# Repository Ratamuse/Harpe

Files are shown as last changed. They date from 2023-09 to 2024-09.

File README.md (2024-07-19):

# Harpe anti frelons à pattes jaunes

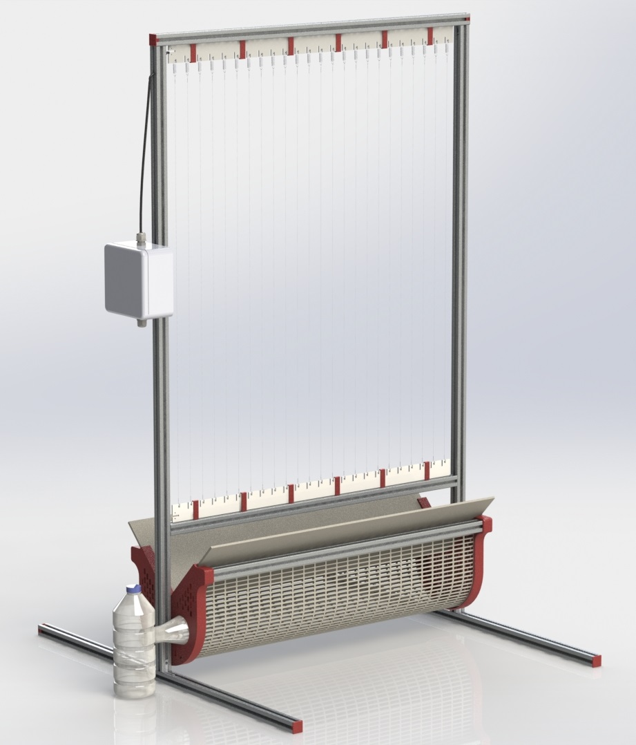
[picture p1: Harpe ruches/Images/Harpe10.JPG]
This is an image


La construction de cette harpe fait suite à différents essais effectués les années passées. Montage en tubes PVC, armature en bois, bac de noyade. Ces solutions, certes peu chères, ne me satisfaisaient pas. Manque de rigidité, vieillessement prématuré, problème de cours circuits, noyades d'insectes et d'abeilles en pagaille etc etc. 
Ce montage n'est pas "LOW COST" et ne peux rivaliser avec les montages fait à partir de tréteaux, tuyaux de récupération ou autre. C'est une compilation de ce qui existe déjà, avec des améliorations et les plans sont disponibles si vous voulez en construire une.  
Ayant eu des soucis de cours circuits par le passé, j'ai ajouté un microntroleur avec capteur de luminosité et d'humidité afin de couper le montage la nuit et lorsque l'humidité est trop forte. 

Vous trouverez ci dessous les liens pour:

- [Liste du materiel](https://github.com/Ratamuse/Harpe/blob/main/Harpe%20ruches/Materiel/Materiel.md)
- [Fichier .STL pour impression 3D](https://github.com/Ratamuse/Harpe/tree/main/Harpe%20ruches%2FFichiers%203d%20%C3%A0%20imprimer)
- [Aide au montage](https://github.com/Ratamuse/Harpe/blob/main/Harpe%20ruches/Montage/Construction.md)
- [Fichiers nécessaires pour fabriquer le circuit imprimé de la harpe](https://github.com/Ratamuse/Harpe/tree/main/Harpe%20ruches/Fichier%20Kicad)
- [Exemple de montage électrique](https://github.com/Ratamuse/Harpe/blob/main/Harpe%20ruches/Fichier%20Kicad/Harpe_ESP32/PCB.md)
- [Programme pour microcontroleur ESP32](https://github.com/Ratamuse/Harpe/tree/main/Harpe%20ruches/Code%20Arduino)

**Support via PayPal (https://paypal.me/GNUVarioE?country.x=FR&locale.x=fr_FR) Cette harpe vous plait et est efficace. Payez moi un café! ;-) Support via PayPal (https://paypal.me/GNUVarioE?country.x=FR&locale.x=fr_FR)**

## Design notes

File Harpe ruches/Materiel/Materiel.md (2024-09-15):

## Harpe

Dimensions

**Profilés aluminium extrudé 2020 B-Type rainure 6**
- 2x 1050mm
- 2x 500mm
- 1x 660mm
- 1x 620mm

**Fixation:**
- 8x Équerres interne 20 B-Type rainure 6, M5
- 2x tasseaux lourds, B-Type rainure 6, M5
- 2x Vis DIN 912 M5x12

**Impression 3D:**
- 2x capuchons haut
- 4x capuchons bas
- 6x coulisseaux circuit imprimé haut
- 6x coulisseaux longs circuit imprimé bas
- 1x boîte de jonction (si pas boîte du commerce)

**Partie fils**
- 1x circuits imprimés 600mm 24 trous 4 couches
- 1x circuits imprimés 600mm 24 trous crochets
- 24x ressorts d'extension 5x10x0.5mm
- 1x Bobine de fil inox 0.3mm (fil à filer les cadres)

**Partie électrique**
- 1x Boîte de jonction IP55 minimum 115x115x60mm
- 1x Module haute tension 4.2v --> 1800v
- 1x Convertisseur de tension 12V --> 4.2V
- 2x connecteurs WAGO 2 fils
- Câble électrique 2x1.5mm2
- Fer à braser et fil de soudure
- Scotch isolant
- Batterie 12 volts

## Bac de récupération

**Profilés aluminium extrudé 2020 B-Type rainure 6**
- 2x 610mm

**Impression 3D**
- 1x flasque
- 1x flasque "bouteille"

**Fixation:**
- 4x tasseaux lourds, B-Type rainure 6, M5
- 4x Vis DIN 912 M5x12

**Divers**
- 2x grilles à reine Nicot Dadant 10C
- 10x colliers de serrage
- 2x planches 610x200x3mm (bois, PVC, bakélite....)
- 1x bouteille vide style "Badois" ou "San Pelegrino"
- 1x bouteille vide style "Volvic" ou "Cristaline"

## Option panneau solaire
- 1x panneau solaire 10W
- 1x chargeur solaire PWM ou mieux MPPT
- 1x batterie 12V 7AH

## Kit (seulement profilés aluminium et visserie) disponible en achat sur le site Motedis.fr en cliquant sur le lien suivant:

**[Kit permettant de construire une harpe](https://www.motedis.fr/shop/create_offers_kit.php?oID=809841)**

Cliquez sur "ok" fenêtre "Langue/Paramètres régionaux" puis allez sur panier. Vous pouvez choisir le nombre de kits à commander en haut de la liste. 
Vous restez libre d'enlever du panier l'item "Idea fee". Cela est proposé par le site pour rénumérer la personne qui à préparé le kit. Il existe d'autres sites pour commander des profilés, je ne suis pas affilié et n'ai aucun intéret avec cette société.

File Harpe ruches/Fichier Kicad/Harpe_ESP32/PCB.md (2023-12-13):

# Carte d'alimentation jusqu'à six harpes:

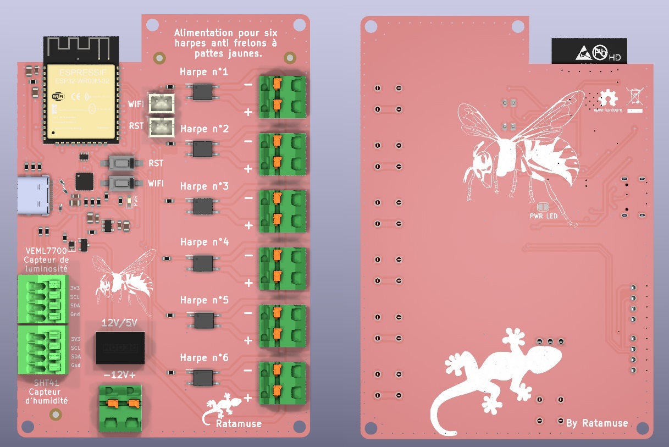
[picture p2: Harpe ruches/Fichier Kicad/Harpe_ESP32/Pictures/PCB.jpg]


La carte doit être alimentée par une batterie 12V. Elle permet d'alimenter de manière cyclique jusqu'à six harpes afin d'économiser de l'énergie et moins soliciter les modules haute tension. 
La carte est équipée de deux connecteurs permettant de brancher:
* un capteur d'humidité SHT41 permettant de couper l'alimentation des harpes en cas de forte humidité.
* un capteur de luminosité permettant de couper les harpes la nuit. 

Les valeurs limites de luminosité, humidité, le nombre de harpes et le rapport cyclique d'alimentation sont modifiables via un serveur web embarqué. 
Pour y accéder il suffit d'appuyer deux secondes sur le bouton "WIFI" (sur la carte ou déporté). Le réseau "harpes" apparaitra comme point d'accès wifi. Le mot de passe pour s'y connecter est 123456789 
Une fois les valeurs modifiées, la carte redemarrera avec les nouveaux paramètres en appuyant sur le bouton "Enregistrer".

Les modules haute tension des harpes consommant en permanence 0.1A, cette manière de les alimenter permet de n'utiliser qu'une petite batterie de 12V 7AH et un panneau solaire de 10W. Un régulateur de charge solaire PWM de 12V, 5 ou 10A sera nécessaire pour recharger la batterie.  

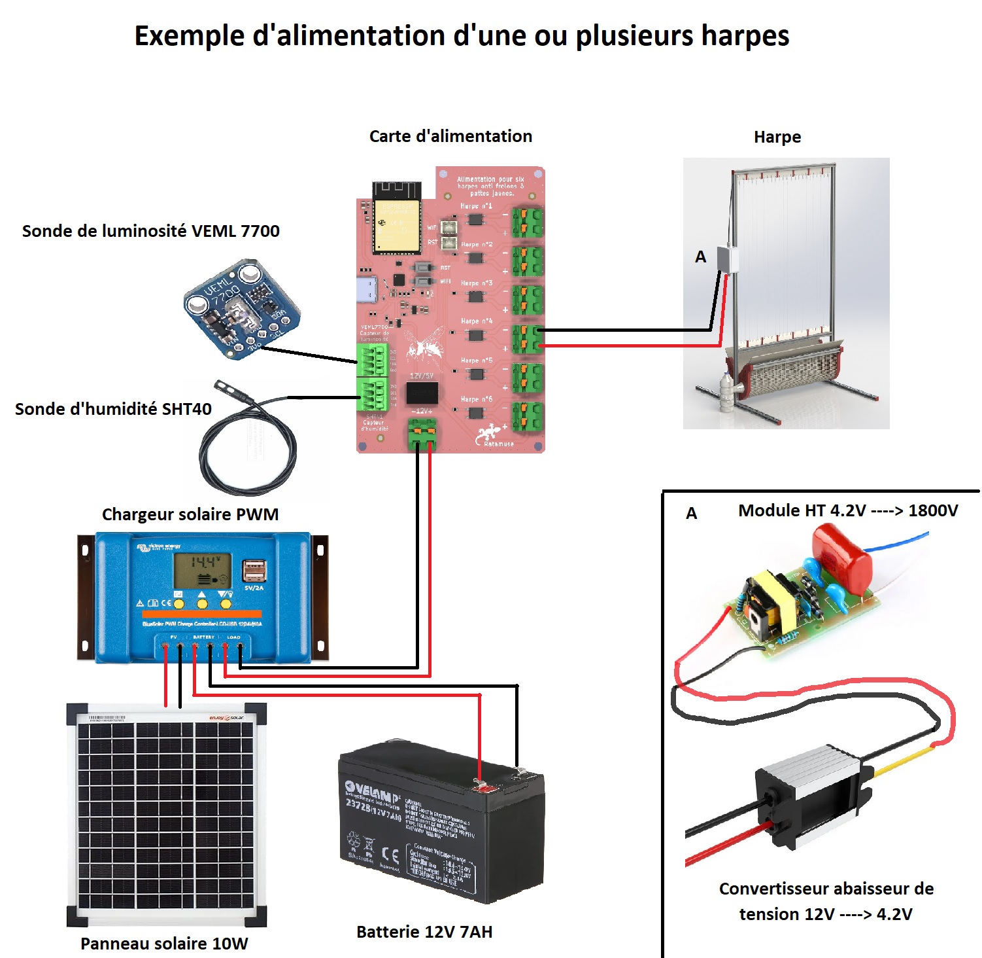
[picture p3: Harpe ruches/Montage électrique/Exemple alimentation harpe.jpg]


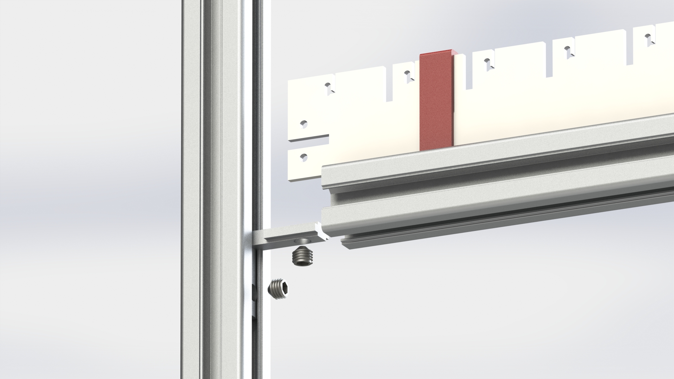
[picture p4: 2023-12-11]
Harpe ruches/Images/Harpe5bis.JPG

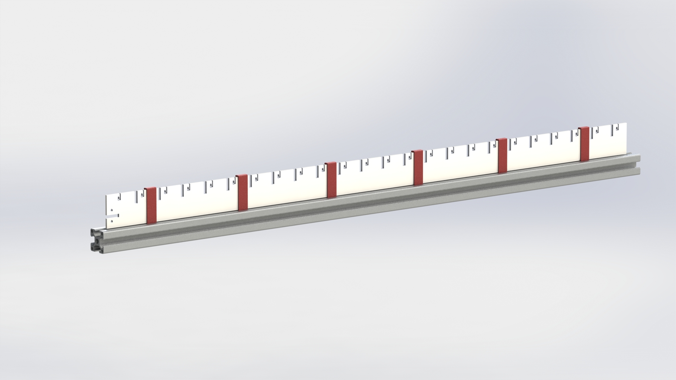
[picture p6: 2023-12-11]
Harpe ruches/Images/Harpe2bis.JPG

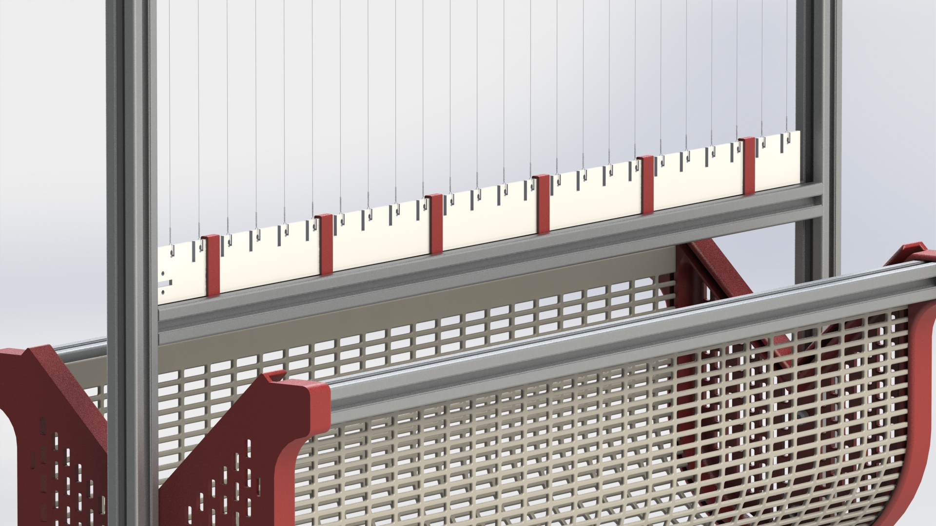
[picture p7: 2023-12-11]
Harpe ruches/Images/Harpe6bis.JPG

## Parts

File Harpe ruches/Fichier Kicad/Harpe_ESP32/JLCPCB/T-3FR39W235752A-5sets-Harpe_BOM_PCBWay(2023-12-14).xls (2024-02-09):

PCBWay Bom Quotation, Product No.:T-3FR39W235752A
Item # | *Designator | *Qty | Manufacturer | *Mfg Part # | Description / Value | *Package/Footprint | *Unit Price(5 sets) | *Total | *Delivery Time | Customer Reply | PCBWay Update
1 | C1,C3 | 2 | Murata | GRM219R61C226ME15L | 16V 22uF X5R ±20% 0805 Multilayer Ceramic Capacitors MLCC | C_0805_2012Metric | $0.291 | $2.910
2 | C2,C7,C9,C11 | 4 | Murata | GCJ188R71C104KA01D | MLCC - CMS 0.1 uF 16 VDC 10% 0603 X7R | C_0603_1608Metric | $0.054 | $1.080
3 | C6 | 1 | Murata | GCM21BR71C475KA73L | MLCC - CMS 4.7 uF 16 VDC 10% 0805 X7R | C_0805_2012Metric | $0.155 | $0.775
4 | R1,R19,R29,R8,R37 | 5 | YAGEO | RT0603BRD0710KL | 100mW Thin Film Resistor ±25ppm/℃ ±0.1% 10kΩ 0603 Chip Resistor - Surface Mount ROHS | R_0603_1608Metric | $0.118 | $2.950
5 | R2,R3,R4,R5,R6,R7,R14 | 7 | YAGEO | RT0603BRD071KL | 100mW Thin Film Resistor ±25ppm/℃ ±0.1% 1kΩ 0603 Chip Resistor - Surface Mount ROHS | R_0603_1608Metric | $0.095 | $3.325
6 | R12 | 1 | YAGEO | RT0603BRD0722K1L | 100mW Thin Film Resistor ±25ppm/℃ ±0.1% 22.1kΩ 0603 Chip Resistor - Surface Mount ROHS | R_0603_1608Metric | $0.147 | $0.735
7 | R13 | 1 | YAGEO | RT0603BRD0747K5L | 100mW Thin Film Resistor ±25ppm/℃ ±0.1% 47.5kΩ 0603 Chip Resistor - Surface Mount ROHS | R_0603_1608Metric | $0.147 | $0.735
8 | U1 | 1 | Espressif | ESP32-WROOM-32E-N4 | ESP32-WROOM-32E-N4 | SMD,18x25.5mm | $4.543 | $22.715
9 | U2,U3,U4,U5,U6,U7 | 6 | Omron Electronics | G3VM-61VY2 |  | SOP254P960X420-4N | $1.030 | $30.900
10 | U12 | 1 | SILICON LABS | CP2102N-A02-GQFN24R | USB转UART UART QFN-24-EP(4x4) USB ICs ROHS | QFN-24-1EP_4x4mm_P0.5mm_EP2.6x2.6mm | $3.140 | $15.700
11 | U13 | 1 | Torex Semicon | XC6220B331MR-G |  | SOT-23-5 | $0.645 | $3.225
12 | R16,R17 | 2 | YAGEO | AT0603BRD072K2L | 100mW Thin Film Resistor ±25ppm/℃ ±0.1% 2.2kΩ 0603 Chip Resistor - Surface Mount ROHS | R_0603_1608Metric | $0.103 | $1.030
13 | D4 | 1 | STMicroelectronics | BAT20JFILM |  | D_SOD-323 | $0.163 | $0.815
14 | Q1 | 1 | ROHM Semicon | UMH3NTN | 100@1mA,5V 2 NPN - Pre-Biased 150mW 100mA 50V SOT-363 | SOT-363_SC-70-6 | $0.114 | $0.570
15 | Q2 | 1 | Diodes Incorporated | DMG2301L-7 | 20V 3A 1.5W 120mΩ@4.5V,2.8A 1.2V@250uA P Channel SOT-23 MOSFETs ROHS | SOT-23 | $0.151 | $0.755
16 | D1,D2,D3 | 3 | Littelfuse | SP1003-01DTG | 7A@8/20us 12V@(Typ) 6V Unidirectional 5V@Max SOD-723 TVS ROHS | SODFL1406X65N | $0.099 | $1.485
17 | J13 | 1 | GCT | USB4105-GF-A | Connectors USB USB Type C,2.0, Rec,SMT, 0.95mmTH Shell Stakes,G/F,RA,Top Mnt,T&R | USB_C_Receptacle_USB2.0 USB4105-GF-A | $1.497 | $7.485
18 | R26 | 1 | YAGEO | RT0603FRE071ML | 100mW Thin Film Resistor ±50ppm/℃ ±1% 1MΩ 0603 Chip Resistor - Surface Mount ROHS | R_0603_1608Metric | $0.084 | $0.420
19 | R33,R34 | 2 | YAGEO | RT0603BRD075K1L | 100mW Thin Film Resistor ±25ppm/℃ ±0.1% 5.1kΩ 0603 | R_0603_1608Metric | $0.094 | $0.940
20 | D15 | 1 | XINGLIGHT | XL-1608VRC-06 | 90mcd 红色透镜 615nm~630nm 正贴 Red 120° 75mW 0603 Light Emitting Diodes (LED) ROHS | LED_0603_1608Metric_Castellated | $0.103 | $0.515
21 | C24,C25 | 2 | Murata | GRM21BR61C106KE15K | 16V 10uF X5R ±10% 0805 Multilayer Ceramic Capacitors MLCC - SMD/SMT ROHS | C_0805_2012Metric | $0.054 | $0.540
 |  |  |  |  |  |  | Component Cost | $99.60
 |  |  |  |  |  |  | Assembly Cost | $30.00
 |  |  |  |  |  |  | PCB Cost | $5.00
 |  |  |  |  |  |  | V1 Member 1% off | -$0.35
 |  |  |  |  |  |  | All Total 5 Sets | $134.25

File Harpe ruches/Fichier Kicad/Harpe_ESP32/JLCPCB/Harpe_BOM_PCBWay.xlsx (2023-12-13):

 |  |  | xxxx xxxx xxxxx xxPCS BOM (Sample Bill of Materials)
Item # | *Designator | *Qty | Manufacturer | *Mfg Part # | Description / Value | *Package/Footprint | Type | Your Instructions / Notes
1 | C1,C3 | 2 | Murata | GRM219R61C226ME15L | 16V 22uF X5R ±20% 0805 Multilayer Ceramic Capacitors MLCC | C_0805_2012Metric
2 | C2,C7,C9,C11 | 4 | Murata | GCJ188R71C104KA01D | MLCC - CMS 0.1 uF 16 VDC 10% 0603 X7R | C_0603_1608Metric
3 | C6 | 1 | Murata | GCM21BR71C475KA73L | MLCC - CMS 4.7 uF 16 VDC 10% 0805 X7R | C_0805_2012Metric
4 | R1,R19,R29,R8,R37 | 5 | YAGEO | RT0603BRD0710KL | 100mW Thin Film Resistor ±25ppm/℃ ±0.1% 10kΩ 0603 Chip Resistor - Surface Mount ROHS | R_0603_1608Metric
5 | R2,R3,R4,R5,R6,R7,R14 | 7 | YAGEO | RT0603BRD071KL | 100mW Thin Film Resistor ±25ppm/℃ ±0.1% 1kΩ 0603 Chip Resistor - Surface Mount ROHS | R_0603_1608Metric
6 | R12 | 1 | YAGEO | RT0603BRD0722K1L | 100mW Thin Film Resistor ±25ppm/℃ ±0.1% 22.1kΩ 0603 Chip Resistor - Surface Mount ROHS | R_0603_1608Metric
7 | R13 | 1 | YAGEO | RT0603BRD0747K5L | 100mW Thin Film Resistor ±25ppm/℃ ±0.1% 47.5kΩ 0603 Chip Resistor - Surface Mount ROHS | R_0603_1608Metric
8 | U1 | 1 | Espressif | ESP32-WROOM-32E-N4 | ESP32-WROOM-32E-N4 | SMD,18x25.5mm
9 | U2,U3,U4,U5,U6,U7 | 6 | Omron Electronics | G3VM-61VY2 |  | SOP254P960X420-4N
10 | U12 | 1 | SILICON LABS | CP2102N-A02-GQFN24R | USB转UART UART QFN-24-EP(4x4) USB ICs ROHS | QFN-24-1EP_4x4mm_P0.5mm_EP2.6x2.6mm
11 | U13 | 1 | Torex Semicon | XC6220B331MR-G |  | SOT-23-5
14 | R16,R17 | 2 | YAGEO | AT0603BRD072K2L | 100mW Thin Film Resistor ±25ppm/℃ ±0.1% 2.2kΩ 0603 Chip Resistor - Surface Mount ROHS | R_0603_1608Metric
15 | D4 | 1 | STMicroelectronics | BAT20JFILM |  | D_SOD-323
16 | Q1 | 1 | ROHM Semicon | UMH3NTN | 100@1mA,5V 2 NPN - Pre-Biased 150mW 100mA 50V SOT-363 | SOT-363_SC-70-6
17 | Q2 | 1 | Diodes Incorporated | DMG2301L-7 | 20V 3A 1.5W 120mΩ@4.5V,2.8A 1.2V@250uA P Channel SOT-23 MOSFETs ROHS | SOT-23
18 | D1,D2,D3 | 3 | Littelfuse | SP1003-01DTG | 7A@8/20us 12V@(Typ) 6V Unidirectional 5V@Max SOD-723 TVS ROHS | SODFL1406X65N
19 | J13 | 1 | GCT (https://www.mouser.fr/manufacturer/gct/) | USB4105-GF-A | Connectors USB USB Type C,2.0, Rec,SMT, 0.95mmTH Shell Stakes,G/F,RA,Top Mnt,T&R | USB_C_Receptacle_USB2.0 USB4105-GF-A
20 | R26 | 1 | YAGEO | RT0603FRE071ML | 100mW Thin Film Resistor ±50ppm/℃ ±1% 1MΩ 0603 Chip Resistor - Surface Mount ROHS | R_0603_1608Metric
21 | R33,R34 | 2 | YAGEO | RT0603BRD075K1L | 100mW Thin Film Resistor ±25ppm/℃ ±0.1% 5.1kΩ 0603 | R_0603_1608Metric
22 | D15 | 1 | XINGLIGHT | XL-1608VRC-06 | 90mcd 红色透镜 615nm~630nm 正贴 Red 120° 75mW 0603 Light Emitting Diodes (LED) ROHS | LED_0603_1608Metric_Castellated
23 | C24,C25 | 2 | Murata | GRM21BR61C106KE15K | 16V 10uF X5R ±10% 0805 Multilayer Ceramic Capacitors MLCC - SMD/SMT ROHS | C_0805_2012Metric
Need a quick and accurante quote? Need an efficient production? Please read SMT Ordering Necessary Files & Info in 1 minute. Thank you very much! (https://www.pcbway.com/smt_ordering_guide.html)
Click for Instructions on How to Create a BOM (https://www.pcbway.com/blog/PCB_Assembly/How_to_Build_a_BOM__Bill_Of_Materials_.html)

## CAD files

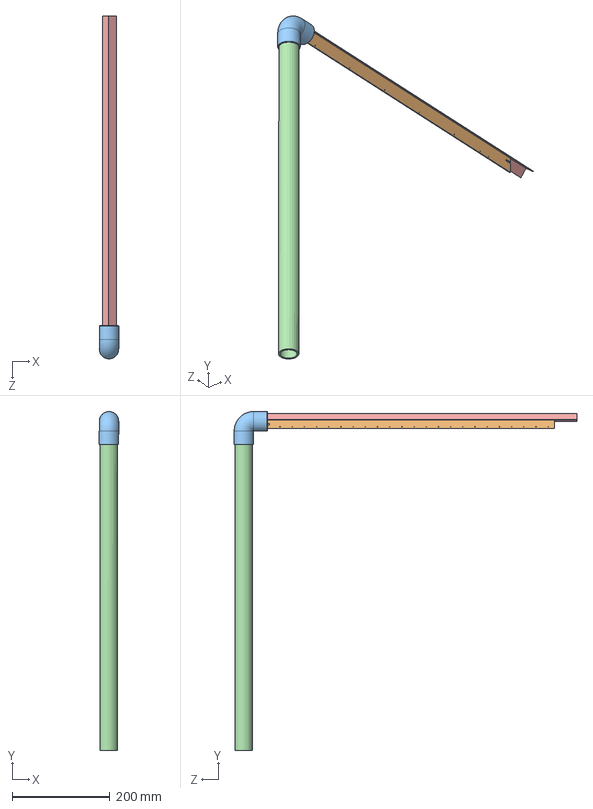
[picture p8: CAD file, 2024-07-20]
Harpe ruches/Fichier Kicad/Harpe ruches bas sans cuivre/Harpe.SLDASM
40.1 x 695.2 x 702.9 mm
fixation pcb ruche
Harpe ruches
tube 32 x600
equerre_egale_635

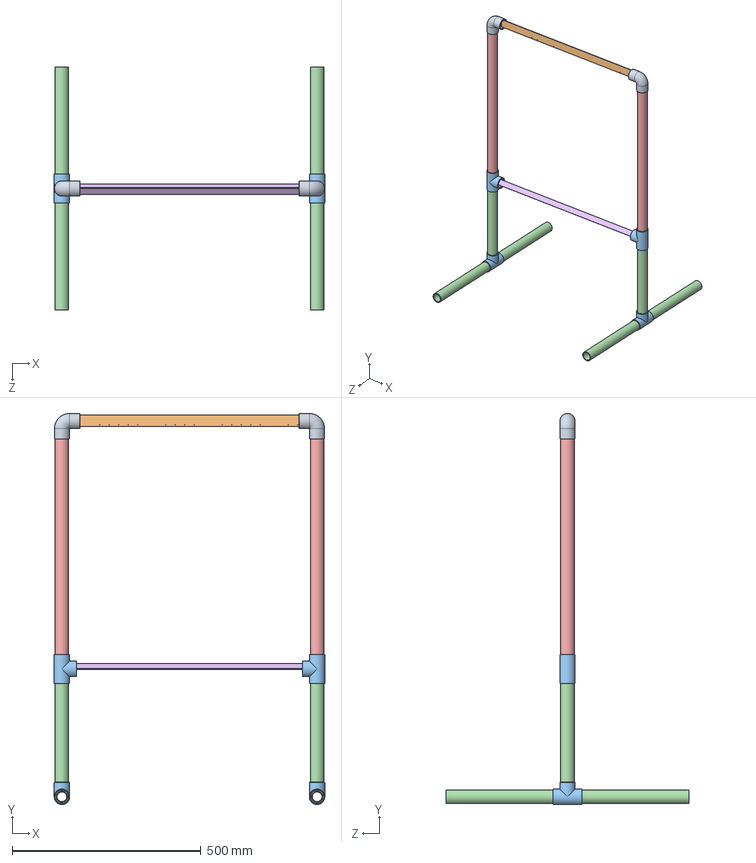
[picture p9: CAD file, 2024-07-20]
Harpe ruches/Fichier Kicad/Harpe ruches bas sans cuivre/harpe frelon/Harpe 2.0.SLDASM
717.7 x 1037.2 x 644.0 mm
PCB harpe
tube 32 x250 x 6
tube 32 x600 x 2
equerre_egale_635

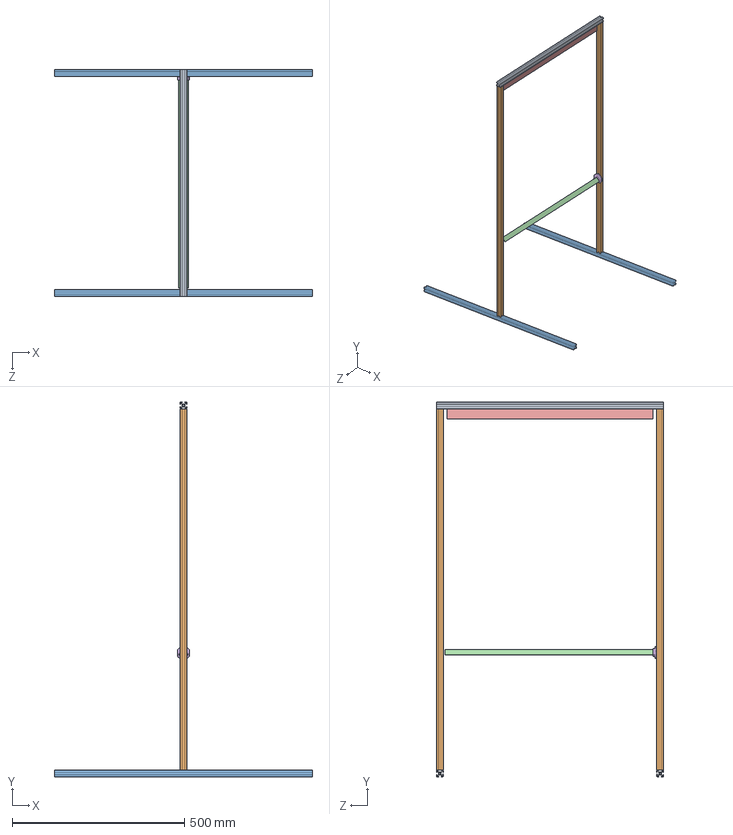
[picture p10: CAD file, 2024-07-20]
Harpe ruches/Fichier Kicad/Harpe ruches bas sans cuivre/harpe frelon/harpe alu/Harpe_V3.SLDASM
750.0 x 1090.0 x 660.0 mm
profilé 660x20
profilé 1050x20 x 2
profilé 750x20 x 2
equerre_egale_620x2
pcb 600x30x2
accroche equerre

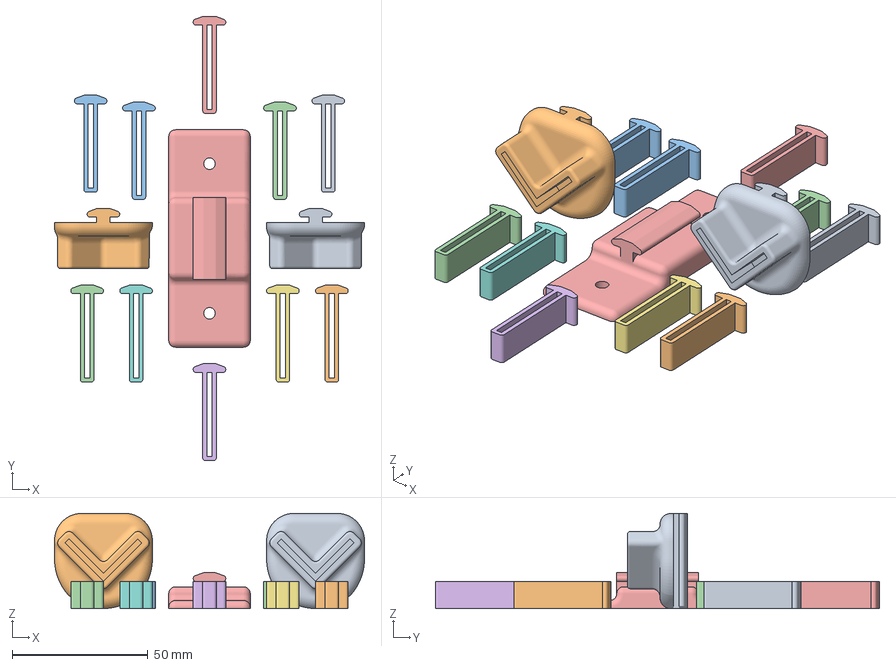
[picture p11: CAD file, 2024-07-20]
Harpe ruches/Fichier Kicad/Harpe ruches bas sans cuivre/harpe frelon/harpe alu/Kit ruche blanc_equerre & PCB.3mf
114.0 x 163.4 x 35.0 mm
accroche equerre.STL
accroche pcb.STL
support boite harpe.STL

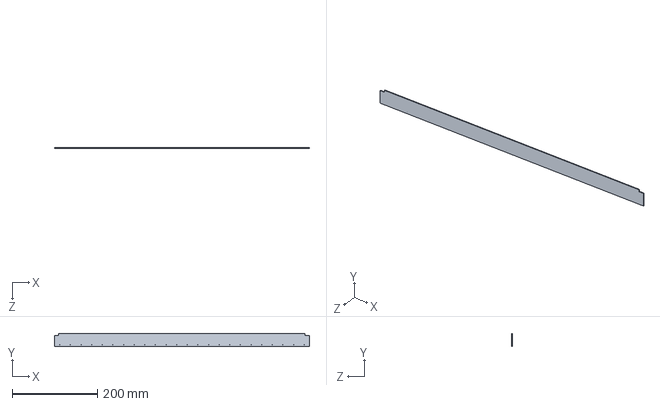
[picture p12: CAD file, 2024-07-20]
Harpe ruches/Fichier Kicad/Harpe ruches bas sans cuivre/harpe frelon/PCB harpe.SLDPRT
600.0 x 30.0 x 1.60 mm

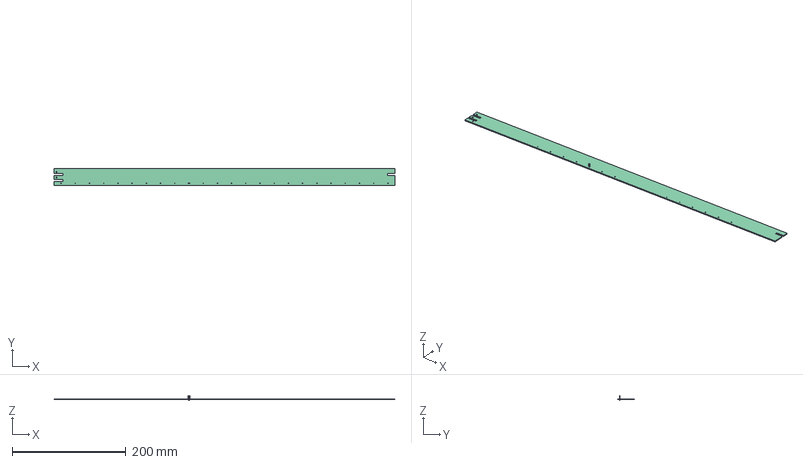
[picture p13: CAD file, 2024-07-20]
Harpe ruches/Fichier Kicad/Harpe ruches bas sans cuivre/Harpe_ruches_union.FCStd
600.0 x 30.0 x 8.50 mm
Pcb_4bcc
REF_Pin_d1.4mm_L8.5mm_W2.8mm_FlatFork_ccd2f83154d6

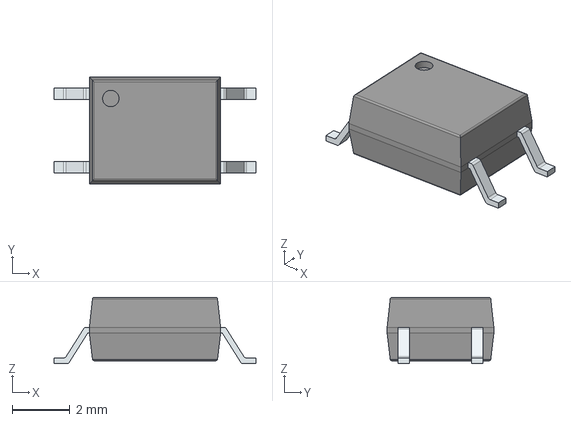
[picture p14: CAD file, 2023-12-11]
Harpe ruches/Fichier Kicad/Harpe_ESP32/3D/G3VM-61VY2.stp
7.00 x 3.70 x 2.30 mm
PinsArrayLR

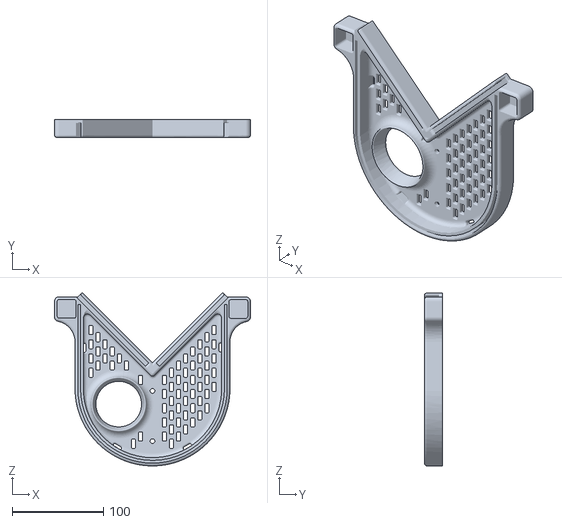
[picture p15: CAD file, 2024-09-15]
Harpe ruches/Fichiers 3d à imprimer/Flasque bouteille v3.STL
214.7 x 20.0 x 189.4

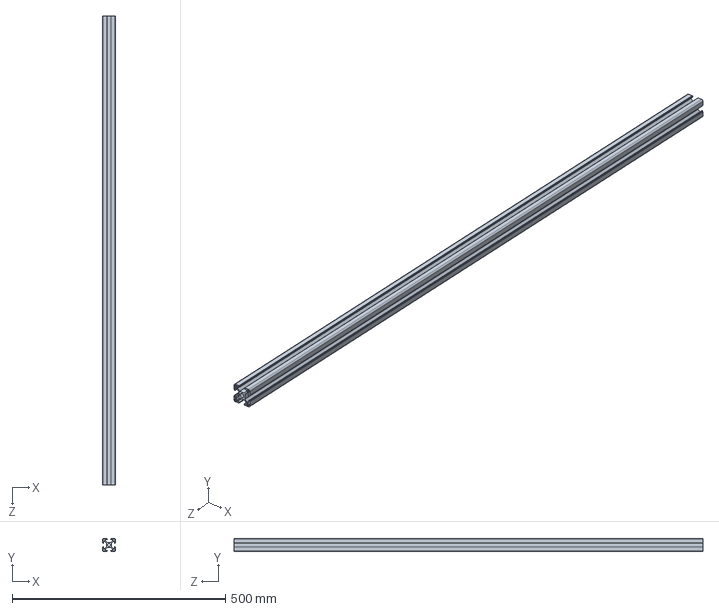
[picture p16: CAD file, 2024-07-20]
Harpe ruches/Fichier Kicad/Harpe ruches bas sans cuivre/harpe frelon/harpe alu/profilé 1100x30.SLDPRT
30.0 x 30.0 x 1100.0 mm

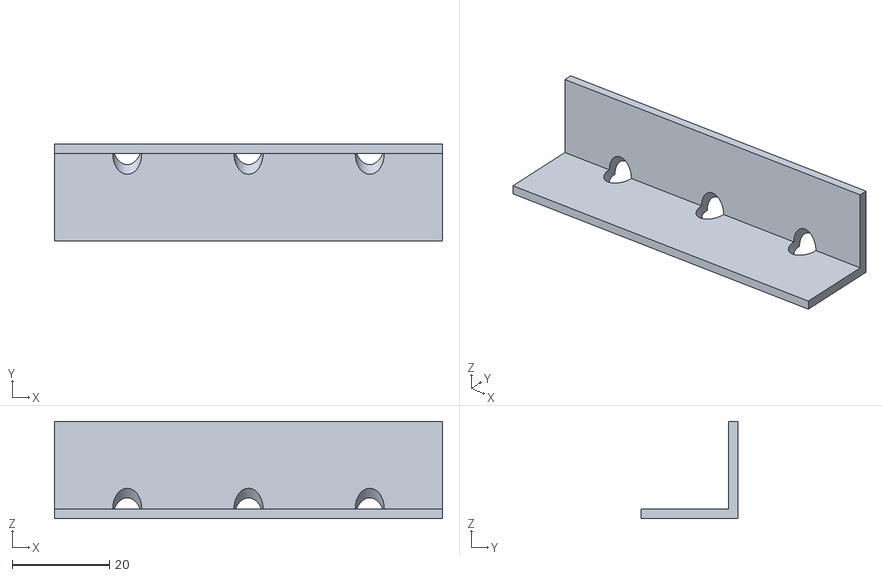
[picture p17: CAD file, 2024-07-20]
Harpe ruches/Fichier Kicad/Harpe ruches bas sans cuivre/harpe frelon/équerre_20mm.STL
80.0 x 20.0 x 20.0

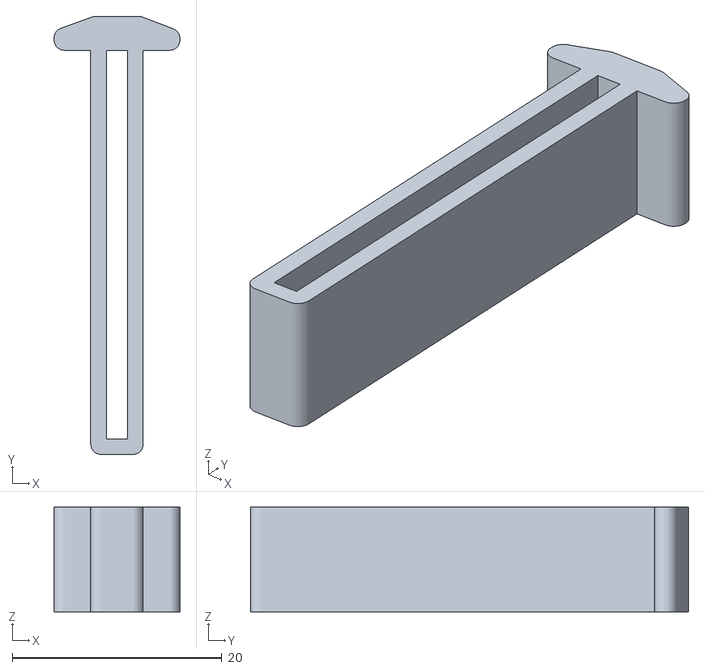
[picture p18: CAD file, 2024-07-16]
Harpe ruches/Fichiers 3d à imprimer/coulisseau circuit imprimé long.STL
12.0 x 41.7 x 10.0

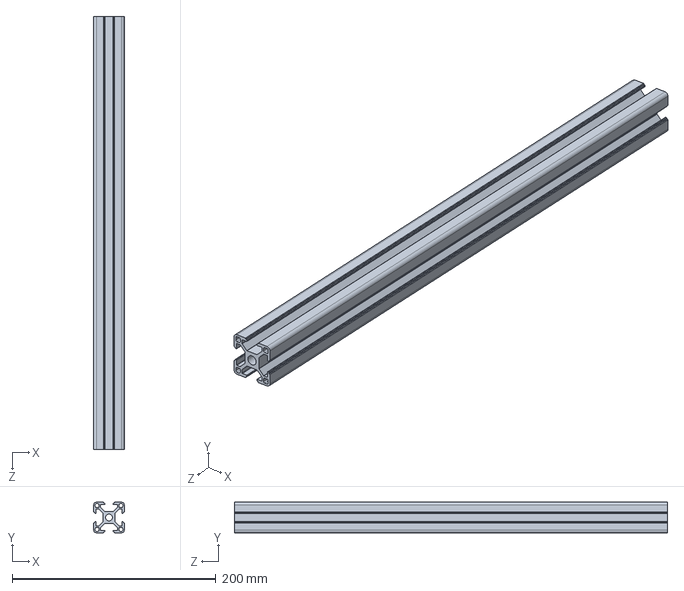
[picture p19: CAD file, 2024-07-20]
Harpe ruches/Fichier Kicad/Harpe ruches bas sans cuivre/harpe frelon/harpe alu/profilé 850x30.SLDPRT
30.0 x 30.0 x 425.0 mm

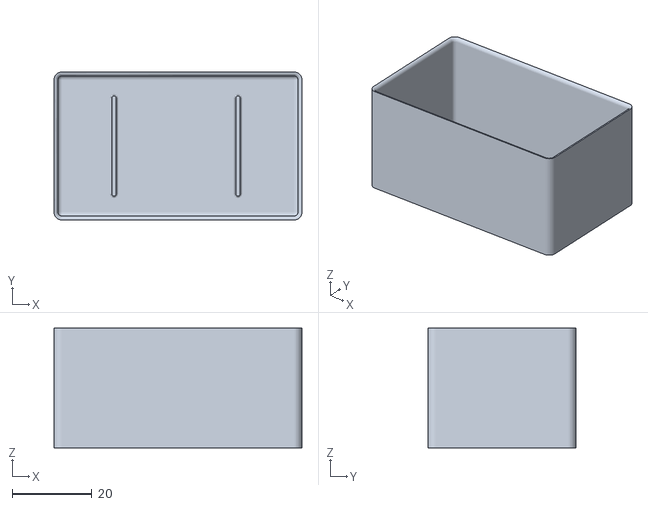
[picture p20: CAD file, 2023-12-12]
Harpe ruches/Fichiers 3d à imprimer/Resine module HT.STL
62.0 x 37.0 x 30.0

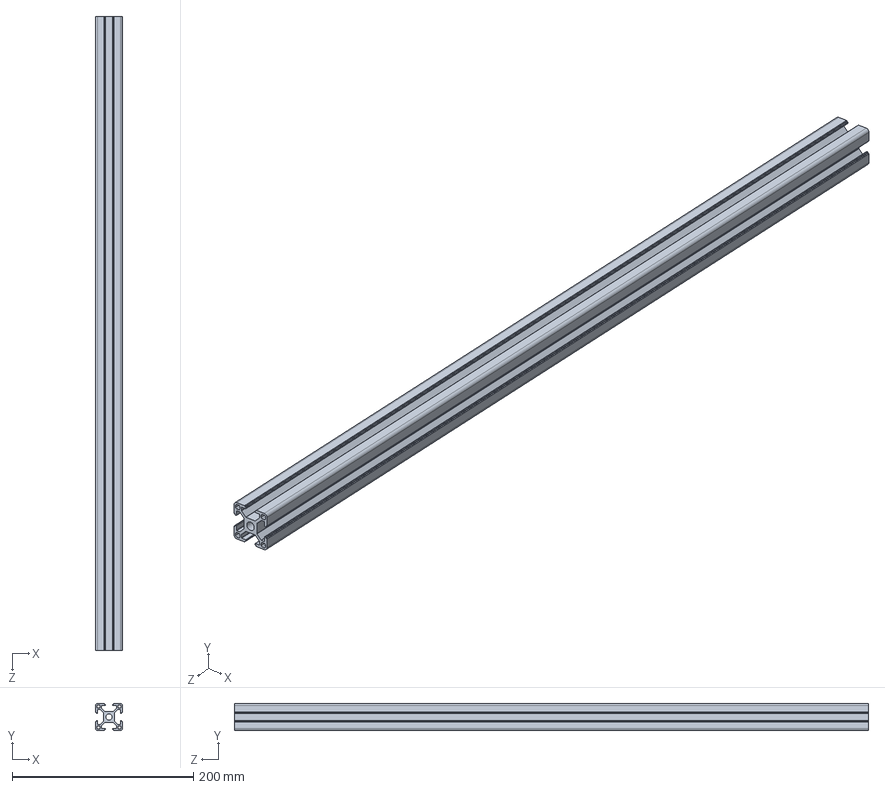
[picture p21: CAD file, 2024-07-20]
Harpe ruches/Fichier Kicad/Harpe ruches bas sans cuivre/harpe frelon/harpe alu/profilé 700x30.SLDPRT
30.0 x 30.0 x 700.0 mm

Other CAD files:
Harpe ruches/Fichier Kicad/Harpe ruches bas sans cuivre/Harpe_ruches1_union.FCStd
Harpe ruches/Fichier Kicad/Harpe ruches bas sans cuivre/harpe frelon/Harpe ruches.step
Harpe ruches/Fichier Kicad/Harpe ruches bas sans cuivre/Harpe ruches.step
Harpe ruches/Fichier Kicad/Harpe ruches bas sans cuivre/harpe frelon/tube 32 x600 percé.SLDPRT
Harpe ruches/Fichier Kicad/Harpe ruches bas sans cuivre/Harpe ruches.SLDPRT
Harpe ruches/Fichier Kicad/Harpe ruches bas sans cuivre/harpe frelon/05_03_032.SLDPRT
Harpe ruches/Fichier Kicad/Harpe ruches bas sans cuivre/harpe frelon/36_01_032.SLDPRT
Harpe ruches/Fichier Kicad/Harpe ruches bas sans cuivre/harpe frelon/Harpe ruches.SLDASM
Harpe ruches/Fichier Kicad/Harpe ruches bas sans cuivre/harpe frelon/Pièce1.SLDPRT
Harpe ruches/Fichier Kicad/Harpe ruches bas sans cuivre/harpe frelon/Pièce1.STL
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

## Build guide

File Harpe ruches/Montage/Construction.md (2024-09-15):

# Assemblage de la harpe

Dimensions

1/ Commencez par insérer les 6 coulisseaux supportant le circuit imprimé dans le profilé de 660mm et les 6 coulisseaux supportant le cicuit imprimé dans le profilé de 620mm.

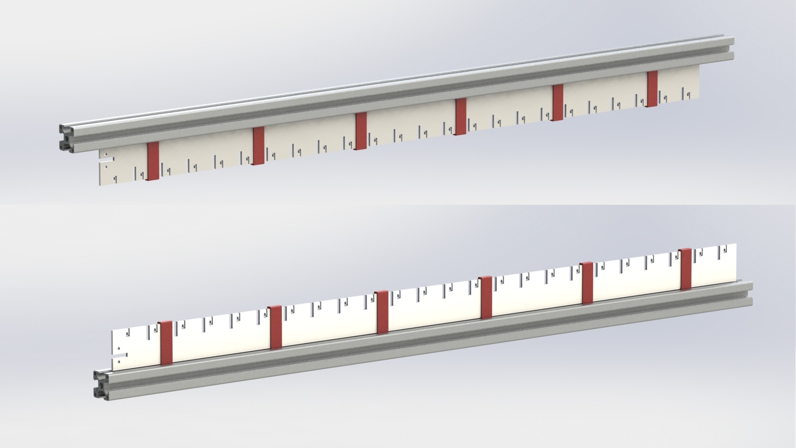
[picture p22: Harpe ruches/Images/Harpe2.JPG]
This is an image


2/ Fixez ces deux profilés aux deux profilés de 1050mm à l'aide des équerres.
   Enfoncez les capuchons en bout du profilé de 660mm. 

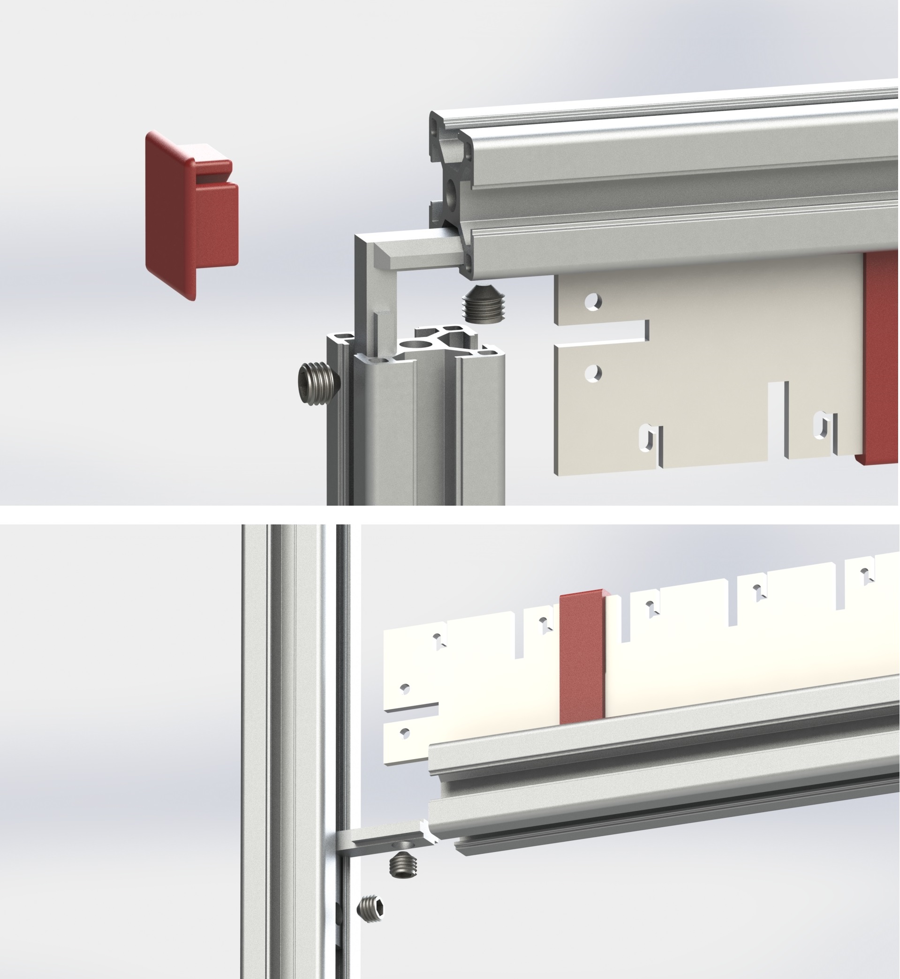
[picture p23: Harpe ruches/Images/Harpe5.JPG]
This is an image


3/ Montez le bac de récupération en enfoncant les deux profilés de 610mm dans les encoches des flasques. Puis à l'aide de coliers en plastique fixez une des grilles à reine dans une flasque puis faites de même avec l'autre grille à reine et l'autre flasque. Utilisez d'autres coliers pour aligner et maintenir en place les deux grilles.
   Vissez les vis et tasseaux lourds sans les serrer pour faciliter la mise en place dans les profilés de 1050mm. 
  
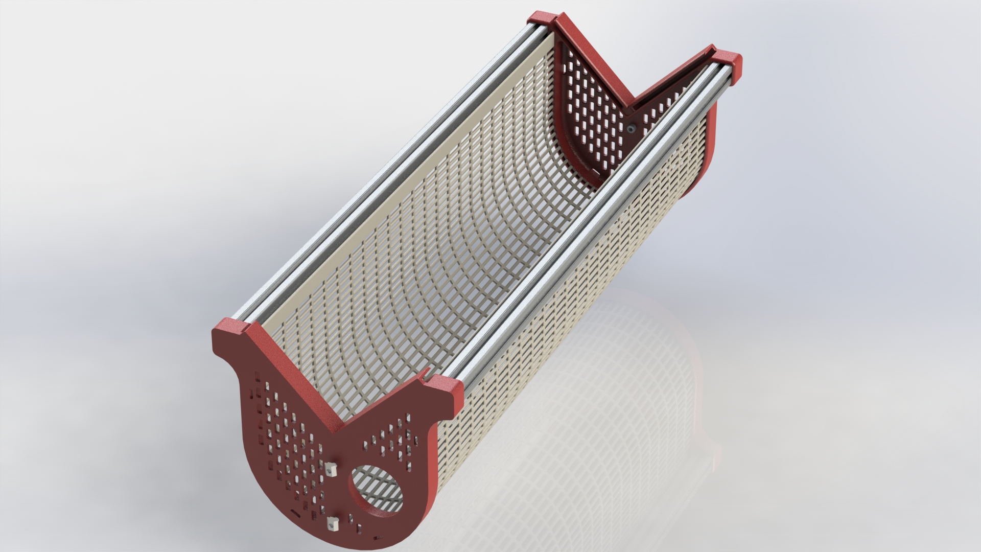
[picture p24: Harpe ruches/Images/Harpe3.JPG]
This is an image


4/ Percez 2 trous à l'arrière de la boîte de jonction afin de fixer les vis et tasseaux lourds. Glissez la boîte de jonction sur le profilé de 1050mm coté trous de connexion électrique du circuit imprimé.

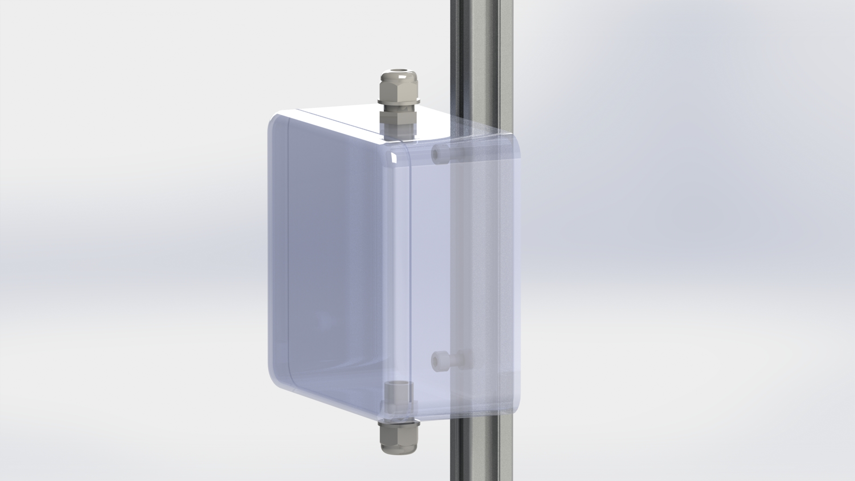
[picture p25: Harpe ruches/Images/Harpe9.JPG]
This is an image
  

5/ Glissez le bac de récupération entre les deux montants de 1050mm et serrez les vis au niveau désiré. 

   Pour les pieds de la harpe, fixez les deux profilés de 500mm à l'aide des 4 équerres restantes. Enfoncez les 4 capuchons au bout des profilés. 

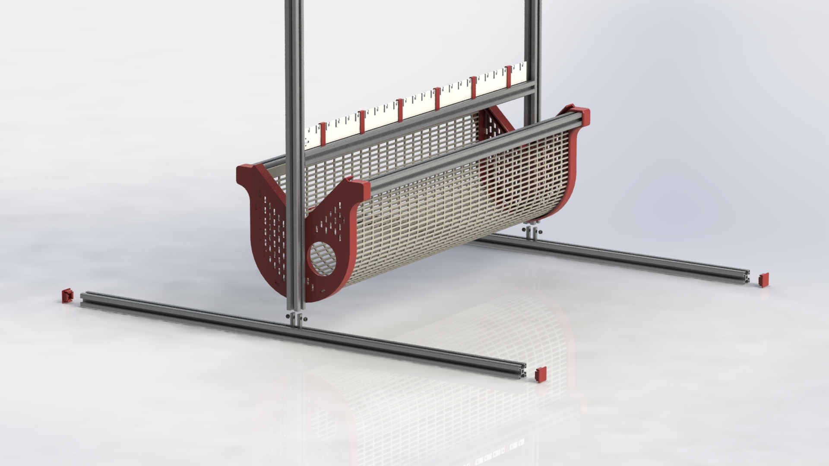
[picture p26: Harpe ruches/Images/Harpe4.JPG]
This is an image
  

6/ Accrochez les ressorts sur le circuit imprimé supérieur puis accrochez les fils entre les ressorts et le circuit imprimé inférieur. Réglez la hauteur du profilé de 610mm en fonction de la longueur des fils désirée.   
   Une fois tous les fils accrochés, descendez doucement le profil de 610mm en desserant les vis des équerres. Ressérez les vis une fois les ressorts légèrement tendus. Puis ajustez la tension des fils en utilisant une pince zig zag.

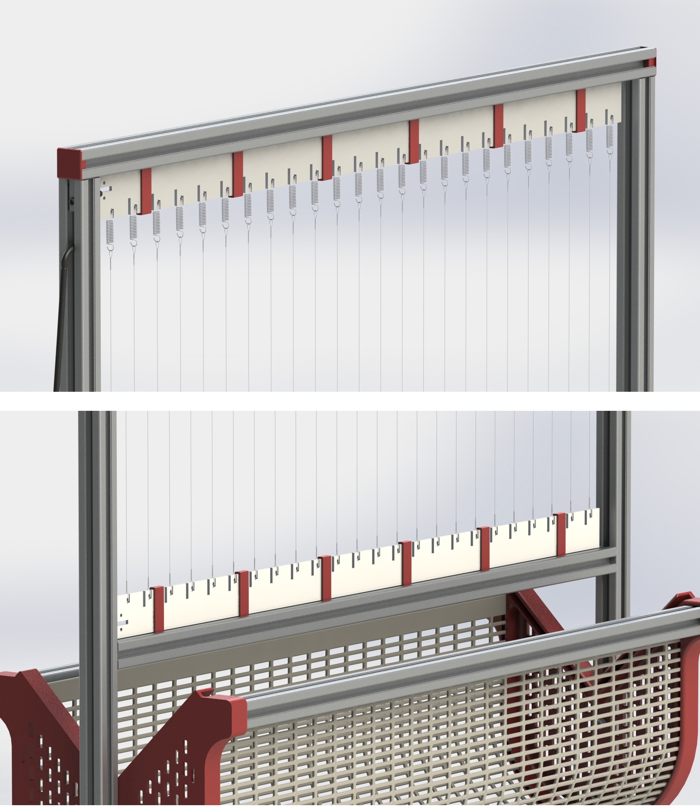
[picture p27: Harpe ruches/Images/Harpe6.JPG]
This is an image


7/ Coupez un fil électrique de 2x1.5mm². D'un coté passez le dans la boîte de jonction par un presse étoupe si vous en avez ou percez en trou dans la membrane de la boîte (plutôt coté bas). Soudez l'autre coté du fil au circuit imprimé. Vous pouvez percer un trou de 5mm dans le profilé de 1050mm pour faire passer le fil. 

8/ Coupez une bouteille de "Badois" ou "San Pelegrino" à 10cm du goulot puis collez la avec de l'araldite ou colle cyano à la flasque prévue à cet effet. Percez un trou du diamètre du goulot dans une autre bouteille plastique et clipsez la au goulot.  

This is an image

# Fabrication des fils

Sur une planche de bois, plantez deux clous (sans tête) à une distance correspondant à la longueur de fil souhaitée. Puis servez vous en pour créer des boucles à distance constante.

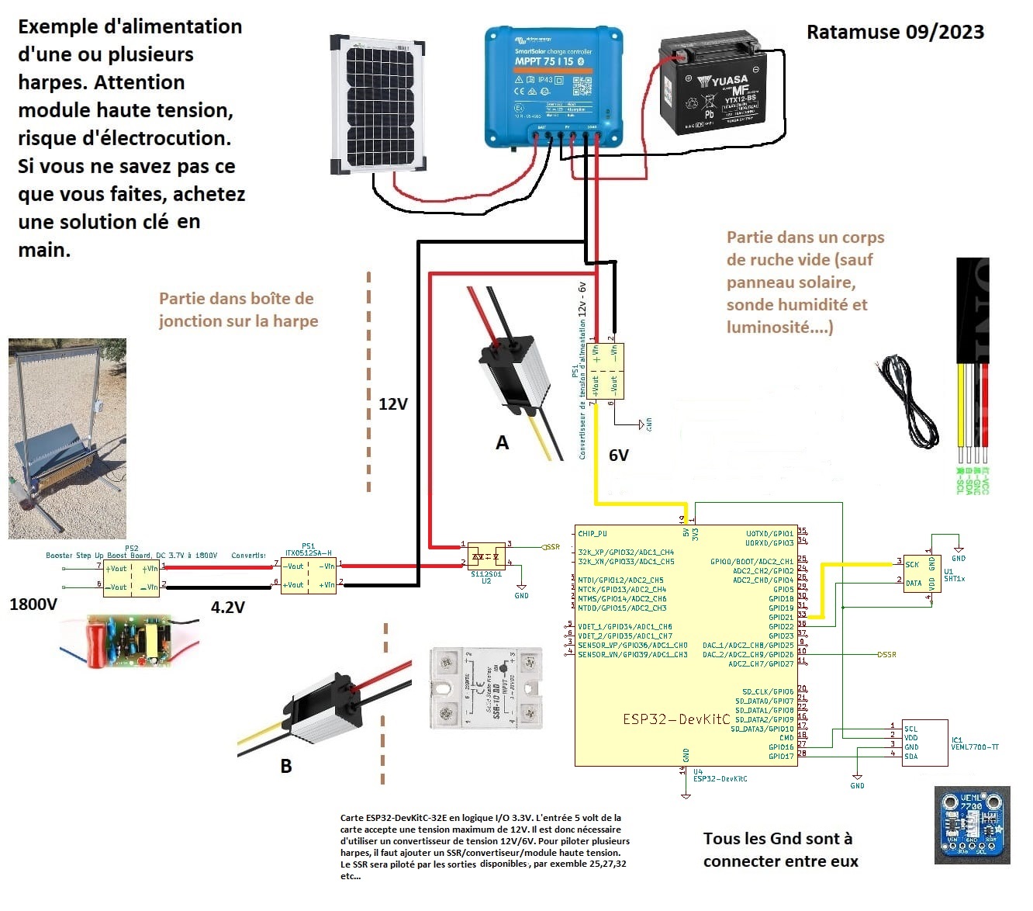
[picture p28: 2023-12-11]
Harpe ruches/Montage électrique/Montage électrique.jpg

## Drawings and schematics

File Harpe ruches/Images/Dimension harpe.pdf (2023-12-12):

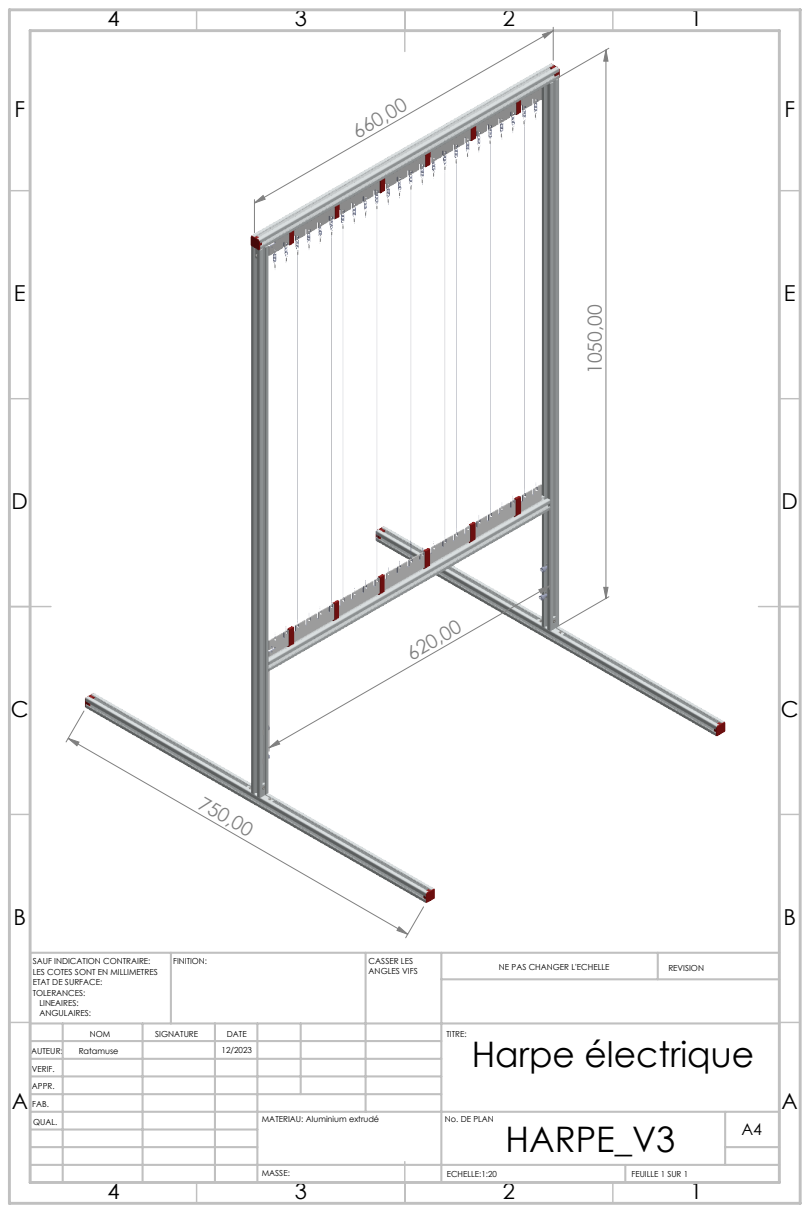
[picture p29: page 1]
FINITION:; CASSER LES; ANGLES VIFS; NE PAS CHANGER L'ECHELLE; REVISION; ECHELLE:1:20; FEUILLE 1 SUR 1

SAUF INDICATION CONTRAIRE:
LES COTES SONT EN MILLIMETRES
ETAT DE SURFACE:
TOLERANCES:
LINEAIRES:
ANGULAIRES:

NOM | SIGNATURE | DATE | | | | TITRE: Harpe électrique

AUTEUR: | Ratamuse | | 12/2023
VERIF.
APPR.
FAB.
QUAL. | | | | MATERIAU: Aluminium extrudé | No. DE PLAN HARPE_V3 | A4

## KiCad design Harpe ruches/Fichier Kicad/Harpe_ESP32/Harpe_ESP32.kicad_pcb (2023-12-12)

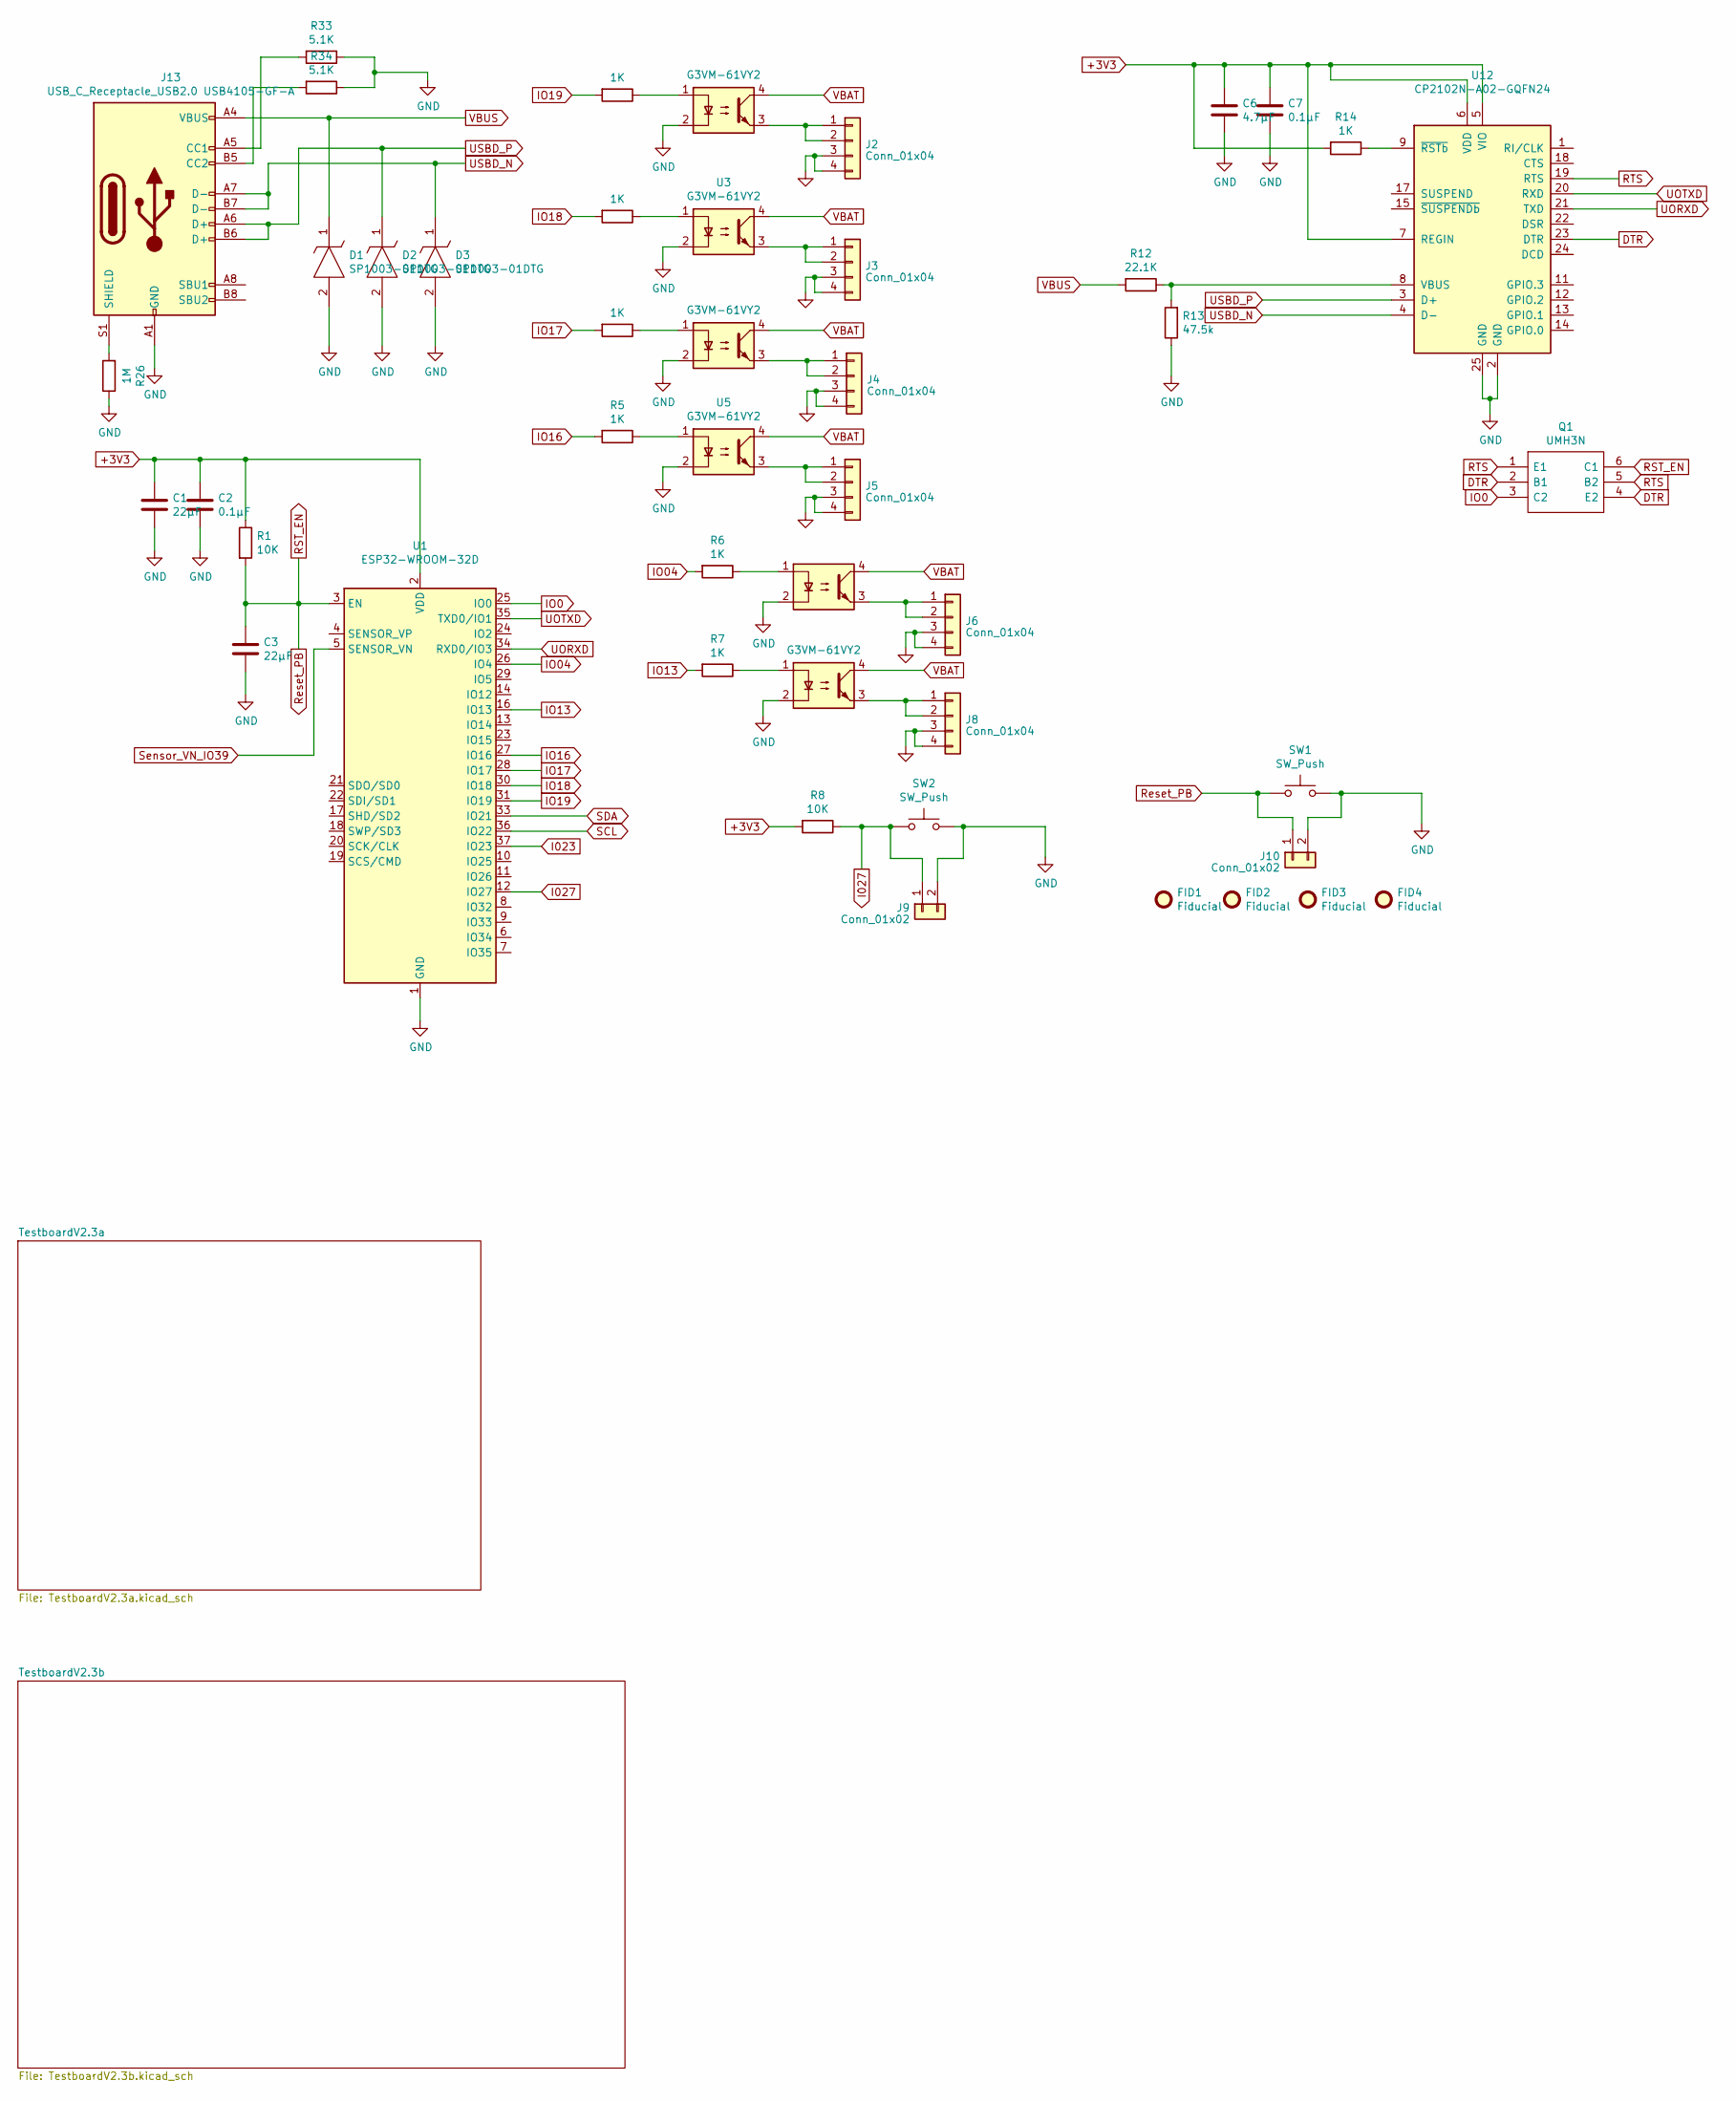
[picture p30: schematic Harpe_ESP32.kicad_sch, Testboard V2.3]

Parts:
C1: 22µF; 1190297
C2, C7: 0.1µF; C_0603_1608Metric
C3: 22µF; C_0805_2012Metric
C6: 4.7µF; C_0805_2012Metric
D1, D2, D3: SP1003-01DTG; SODFL1406X65N; Manufacturer_Part_Number SP1003-01DTG; Mouser Part Number 576-SP1003-01DTG
FID1, FID2, FID3, FID4: Fiducial; Fiducial_1.5mm_Mask3mm
J2, J3, J4, J5, J6, J8: Conn_01x04; 1862411
J9, J10: Conn_01x02; JST_PH_B2B-PH-K_1x02_P2.00mm_Vertical
J13: USB_C_Receptacle_USB2.0 USB4105-GF-A; TYPE-C-31-M-12
Q1: UMH3N; SOT-363_SC-70-6; Manufacturer_Part_Number UMH3N
R1, R8: 10K; R_0603_1608Metric
R2, R3, R4, R5, R6, R7, R14: 1K; R_0603_1608Metric
R12: 22.1K; R_0603_1608Metric
R13: 47.5k; R_0603_1608Metric
R26: 1M; R_0603_1608Metric
R33, R34: 5.1K; R_0603_1608Metric
SW1, SW2: SW_Push; PTS636SL43SMTRLFS
U1: ESP32-WROOM-32D; ESP32WROOM32EM113EH2800PH3Q0
U2, U3, U4, U5, U6, U7: G3VM-61VY2; SOP254P700X230-4N
U12: CP2102N-A02-GQFN24; QFN-24-1EP_4x4mm_P0.5mm_EP2.6x2.6mm

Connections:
+3V3: C1.1, C2.1, C6.1, C7.1, R1.1, R8.2, R14.2, U1.2 (VDD), U12.5 (VIO), U12.6 (VDD), U12.7 (REGIN); also elsewhere on the board
DTR: Q1.2 (B1), Q1.4 (E2), U12.23 (DTR)
I023: U1.37 (IO23)
I027: J9.1, R8.1, SW2.1, U1.12 (IO27)
IO0: Q1.3 (C2), U1.25 (IO0)
IO04: R6.2, U1.26 (IO4)
IO13: R7.2, U1.16 (IO13)
IO16: R5.2, U1.27 (IO16)
IO17: R4.2, U1.28 (IO17)
IO18: R3.2, U1.30 (IO18)
IO19: R2.2, U1.31 (IO19)
unnamed: J2.1, J2.2, U2.3
unnamed: J3.1, J3.2, U3.3
unnamed: J4.1, J4.2, U4.3
unnamed: J5.1, J5.2, U5.3
unnamed: J6.1, J6.2, U6.3
unnamed: J13.A5 (CC1), R33.2
unnamed: J13.B5 (CC2), R34.2
unnamed: J13.S1 (SHIELD), R26.2
unnamed: R2.1, U2.1
unnamed: R3.1, U3.1
unnamed: R4.1, U4.1
unnamed: R5.1, U5.1
unnamed: R6.1, U6.1
unnamed: R7.1, U7.1
unnamed: R12.1, R13.2, U12.8 (VBUS)
unnamed: R14.1, U12.9 (~RSTb)
RST_EN: C3.1, J10.1, Q1.6 (C1), R1.2, SW1.1, U1.3 (EN)
RTS: Q1.1 (E1), Q1.5 (B2), U12.19 (RTS)
SCL: U1.36 (IO22); also elsewhere on the board
SDA: U1.33 (IO21); also elsewhere on the board
Sensor_VN_IO39: U1.5 (SENSOR_VN)
UORXD: U1.34 (RXD0/IO3), U12.21 (TXD)
UOTXD: U1.35 (TXD0/IO1), U12.20 (RXD)
USBD_N: D3.1, J13.A7 (D-), J13.B7 (D-), U12.4 (D-)
USBD_P: D2.1, J13.A6 (D+), J13.B6 (D+), U12.3 (D+)
VBUS: D1.1, J13.A4 (VBUS), J13.A9 (VBUS), J13.B4 (VBUS), J13.B9 (VBUS), R12.2; also elsewhere on the board

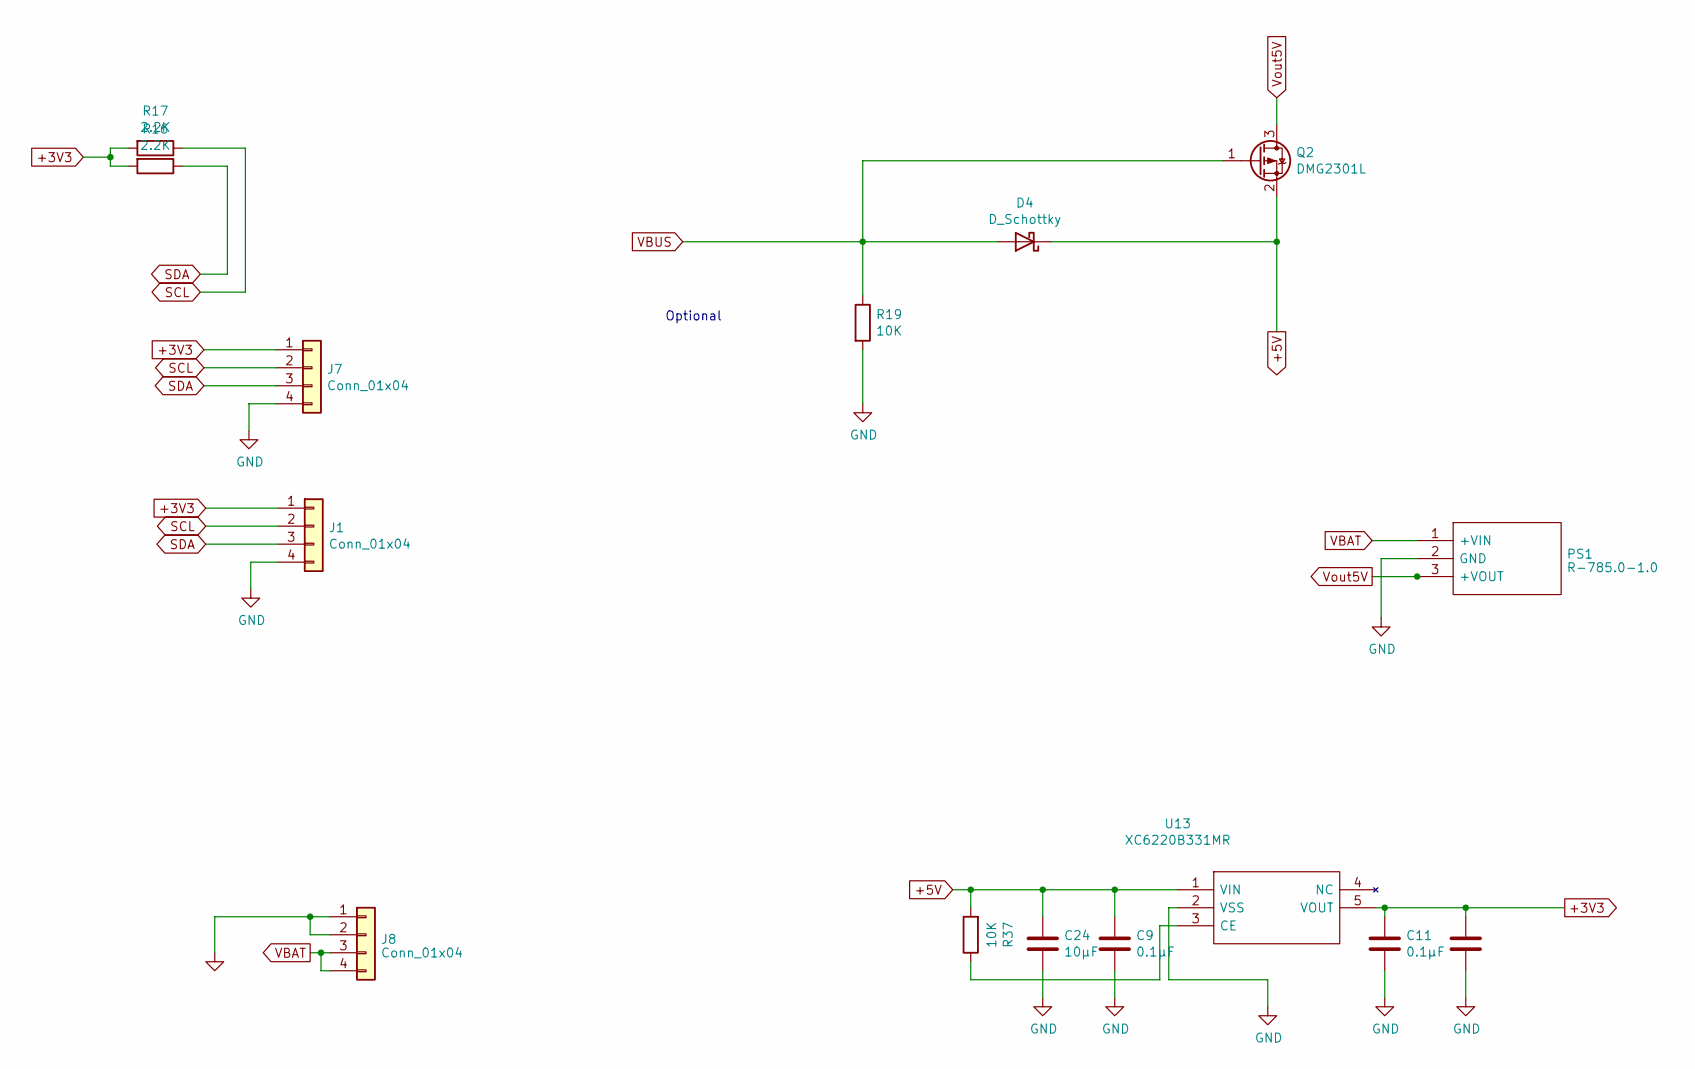
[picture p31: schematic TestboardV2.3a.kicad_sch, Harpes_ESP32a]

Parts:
C9, C11: 0.1µF; C_0603_1608Metric
C24, C25: 10µF; C_0805_2012Metric
D4: D_Schottky; D_SOD-323
J1, J7: Conn_01x04; 1989764
J8: Conn_01x04; 1862411
PS1: R-785.0-1.0; R785010; Mouser Part Number 919-R-785.0-1.0
Q2: DMG2301L; SOT-23
R16, R17: 2.2K; R_0603_1608Metric
R19, R37: 10K; R_0603_1608Metric
U13: XC6220B331MR; SOT-23-5

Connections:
+3V3: C11.1, C25.1, J1.1, J7.1, R16.2, R17.2, U13.5 (VOUT); also elsewhere on the board
+5V: C9.1, C24.1, D4.1 (K), Q2.2 (S), R37.2, U13.1 (VIN)
unnamed: R37.1, U13.3 (CE)
SCL: J1.2, J7.2, R17.1; also elsewhere on the board
SDA: J1.3, J7.3, R16.1; also elsewhere on the board
VBUS: D4.2 (A), Q2.1 (G), R19.1; also elsewhere on the board
Vout5V: PS1.3 (+VOUT), Q2.3 (D)

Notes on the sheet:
Optional

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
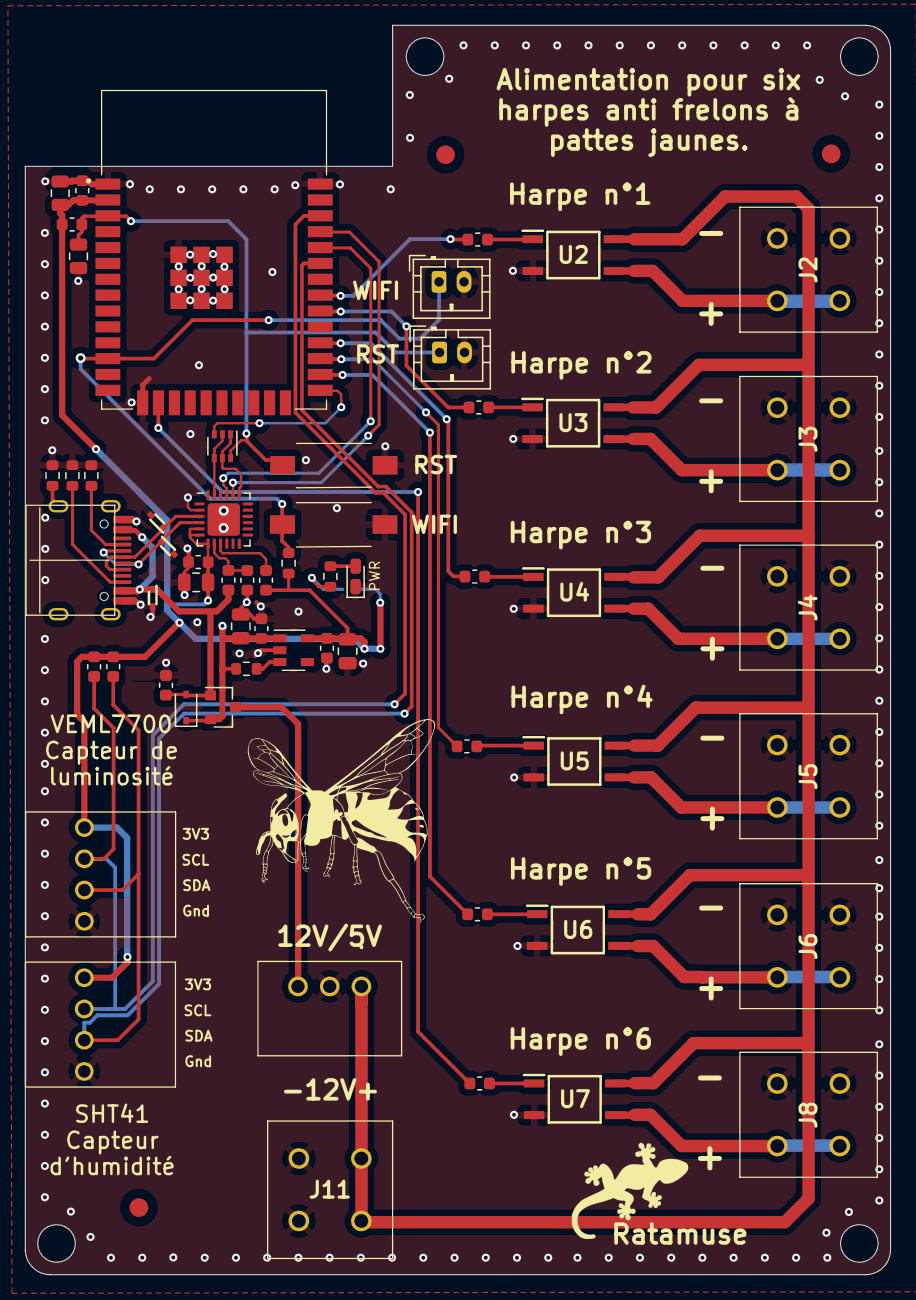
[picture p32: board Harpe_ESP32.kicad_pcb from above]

Board: 2 copper layers, 69.3 x 100.0 mm, 63 parts (1 on the bottom side), 43 nets.

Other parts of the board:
D15: LED Green; LED_0603_1608Metric_Castellated
J11: Conn_01x04; 1862411
JP21: SolderJumper_2_Open; SolderJumper-2_P1.3mm_Open_RoundedPad1.0x1.5mm
R29: 10K; R_0603_1608Metric

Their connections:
+3V3: JP21.1; also elsewhere on the board
unnamed: D15.2, R29.1
unnamed: JP21.2, R29.2

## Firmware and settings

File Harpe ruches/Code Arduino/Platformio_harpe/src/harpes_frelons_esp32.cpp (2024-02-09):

//####################### Ratamuse #######################/
//################## ratamuse.pf@googlemail.com ##################/
//######################### Janvier 2024 ######################/
//#################### ESP32 Devboard 3.3V  ####################/
//######################## Version 1.0.1 #######################/


#include <Arduino.h>
#include <WiFi.h>
#include <WebServer.h>
#include <ArduinoJson.h>
#include <Preferences.h>
#include "freertos/FreeRTOS.h"
#include "freertos/task.h"

const char* ssid = "harpe";
const char* password = "123456789";

#include "Adafruit_VEML7700.h"
#include "SensirionI2CSht4x.h"

Adafruit_VEML7700 veml = Adafruit_VEML7700();
float lux = 0;

SensirionI2CSht4x sht4x;
uint16_t error0;
float temperature0;
float humidity0;
float hum_max = 90;
float lux_min = 10;
char errorMessage[256];

WebServer server(80);

StaticJsonDocument<400> psramDoc;

Preferences preferences;

#define SDA_PIN 21
#define SCL_PIN 22
#define harpe1 19
#define harpe2 18
#define harpe3 17
#define harpe4 16
#define harpe5 4
#define harpe6 13
#define wifi 27
int delayTime = 1000; // Nouvelle variable globale

#define uS_TO_S_FACTOR 1000000ULL
#define TIME_TO_SLEEP 600

bool startWebServer = false;

// États des cases à cocher
bool activateHarpe1 = true;
bool activateHarpe2 = true;
bool activateHarpe3 = true;
bool activateHarpe4 = true;
bool activateHarpe5 = true;
bool activateHarpe6 = true;

// Fonction pour surveiller l'état de la broche WiFi
void checkWiFiPin(void * parameter) {
  for (;;) {
    if (digitalRead(wifi) == LOW) {
      ESP.restart();
    }
    delay(100);
  }
}


void savePreferences() {
  preferences.begin("my-app", false);
  preferences.putFloat("hum_max", hum_max);
  preferences.putFloat("lux_min", lux_min);
  preferences.putInt("delayTime", delayTime); // Enregistrer delayTime
  preferences.putBool("harpe1", activateHarpe1);
  preferences.putBool("harpe2", activateHarpe2);
  preferences.putBool("harpe3", activateHarpe3);
  preferences.putBool("harpe4", activateHarpe4);
  preferences.putBool("harpe5", activateHarpe5);
  preferences.putBool("harpe6", activateHarpe6);
  preferences.end();

  // Redémarrer l'ESP32
  ESP.restart();
}


void loadPreferences() {
  preferences.begin("my-app", false);
  hum_max = preferences.getFloat("hum_max", 90.0);
  lux_min = preferences.getFloat("lux_min", 10.0);
  delayTime = preferences.getInt("delayTime", 1000); // Charger delayTime
  activateHarpe1 = preferences.getBool("harpe1", true);
  activateHarpe2 = preferences.getBool("harpe2", true);
  activateHarpe3 = preferences.getBool("harpe3", true);
  activateHarpe4 = preferences.getBool("harpe4", true);
  activateHarpe5 = preferences.getBool("harpe5", true);
  activateHarpe6 = preferences.getBool("harpe6", true);
  preferences.end();
}


  void handleRoot() {
  String html = "<html><head><meta name='viewport' content='width=device-width, initial-scale=1'><style>body {background-color: #fffacd; color: #000;} h1 {color: #daa520; text-align: center;} form {background-color: #f0e68c; padding: 20px; border-radius: 15px; max-width: 90%; margin: auto;} .input-container {display: flex; justify-content: space-between; align-items: center; margin-bottom: 10px;} input[type=number] {width: 100px;} input[type=submit] {background-color: #daa520; color: white; border: none; padding: 10px 20px; text-decoration: none; margin: 4px 2px; cursor: pointer; border-radius: 4px;}</style></head><body>";
  html += "<h1>Gestion des harpes</h1>";
  html += "<h2>Luminosit&eacute;: " + String(lux, 2) + " lux</h2>";
  html += "<h2>Humidit&eacute;: " + String(humidity0, 2) + " %</h2>";
  html += "<form action='/save' method='post'>";
  html += "<div class='input-container'>Humidit&eacute; Max: <input type='number' step='0.1' name='hum_max' value='" + String(hum_max) + "'></div>";
  html += "<div class='input-container'>Luminosit&eacute; Min: <input type='number' step='0.1' name='lux_min' value='" + String(lux_min) + "'></div>";
  html += "<div class='input-container'>Temps d'alim harpe : <input type='number' name='delayTime' value='" + String(delayTime) + "'></div>";
  html += "<label for='harpe1'>Harpe 1</label> <input type='checkbox' name='harpe1'";
  html += activateHarpe1 ? " checked" : "";
  html += "><br>";
  html += "<label for='harpe2'>Harpe 2</label> <input type='checkbox' name='harpe2'";
  html += activateHarpe2 ? " checked" : "";
  html += "><br>";
  html += "<label for='harpe3'>Harpe 3</label> <input type='checkbox' name='harpe3'";
  html += activateHarpe3 ? " checked" : "";
  html += "><br>";
  html += "<label for='harpe4'>Harpe 4</label> <input type='checkbox' name='harpe4'";
  html += activateHarpe4 ? " checked" : "";
  html += "><br>";
  html += "<label for='harpe5'>Harpe 5</label> <input type='checkbox' name='harpe5'";
  html += activateHarpe5 ? " checked" : "";
  html += "><br>";
  html += "<label for='harpe6'>Harpe 6</label> <input type='checkbox' name='harpe6'";
  html += activateHarpe6 ? " checked" : "";
  html += "><br>";
  html += "<input type='submit' value='Sauvegarder'>";
  html += "</form></body></html>";
  server.send(200, "text/html", html);

}





void handleSave() {
  hum_max = server.arg("hum_max").toFloat();
  lux_min = server.arg("lux_min").toFloat();
  delayTime = server.arg("delayTime").toInt(); // Récupérer la nouvelle valeur de delayTime

  // Récupérer l'état des cases à cocher
  activateHarpe1 = server.hasArg("harpe1");
  activateHarpe2 = server.hasArg("harpe2");
  activateHarpe3 = server.hasArg("harpe3");
  activateHarpe4 = server.hasArg("harpe4");
  activateHarpe5 = server.hasArg("harpe5");
  activateHarpe6 = server.hasArg("harpe6");

  // Enregistrer les préférences
  savePreferences();

  server.send(200, "text/plain", "Settings saved");
}

void pagehtml() {
  Serial.begin(115200);
  preferences.begin("my-app", false);

  WiFi.softAP(ssid, password);
  IPAddress IP = WiFi.softAPIP();
  Serial.print("Point d'accès IP: ");
  Serial.println(IP);

  server.on("/", HTTP_GET, handleRoot);
  server.on("/save", HTTP_POST, handleSave);

  server.begin();
  Serial.println("Web server started");

  Wire.begin(SDA_PIN, SCL_PIN);
  Wire.setClock(100000);
  sht4x.begin(Wire, SHT40_I2C_ADDR_44);

  if (!veml.begin()) {
    Serial.println("Sensor not found");
    while (1);
  }
  Serial.println("Sensor found");
}

void programme() {
  Serial.begin(115200);
  Wire.begin(SDA_PIN, SCL_PIN);
  Wire.setClock(100000);
  pinMode(harpe1, OUTPUT);
  digitalWrite(harpe1, LOW);
  pinMode(harpe2, OUTPUT);
  digitalWrite(harpe2, LOW);
  pinMode(harpe3, OUTPUT);
  digitalWrite(harpe3, LOW);
  pinMode(harpe4, OUTPUT);
  digitalWrite(harpe4, LOW);
  pinMode(harpe5, OUTPUT);
  digitalWrite(harpe5, LOW);
  pinMode(harpe6, OUTPUT);
  digitalWrite(harpe6, LOW);

  esp_sleep_enable_timer_wakeup(TIME_TO_SLEEP * uS_TO_S_FACTOR);

  if (!veml.begin()) {
    Serial.println("Sensor not found");
    while (1);
  }
  Serial.println("Sensor found");
  sht4x.begin(Wire, SHT40_I2C_ADDR_44);
}

void LUX() {
  lux = veml.readLux(VEML_LUX_AUTO);
  Serial.print(lux, 2);
  Serial.println("lux");
}

void sht() {
  error0 = sht4x.measureHighPrecision(temperature0, humidity0);
  Serial.print(humidity0, 2);
  Serial.println("humidité");
}

void setup() {
 
  pinMode(wifi, INPUT);

  if (digitalRead(wifi) == LOW) {
    startWebServer = true;
    loadPreferences(); // Charge les valeurs au démarrage
    pagehtml();
  } else {
     // Créer une nouvelle tâche qui s'exécute sur le deuxième cœur
  xTaskCreatePinnedToCore(
    checkWiFiPin,   /* Fonction pour exécuter */
    "Check WiFi",   /* Nom de la tâche */
    10000,          /* Taille de la pile de la tâche */
    NULL,           /* Paramètre de la tâche */
    1,              /* Priorité de la tâche */
    NULL,           /* Tâche créée */
    0);             /* Numéro du cœur */
    loadPreferences(); // Charge les valeurs au démarrage
    programme();
  }
}

void loop() {
  if (startWebServer) {
    LUX();
    sht();
    server.handleClient();
  } else {
    LUX();
    sht();

if (lux >= lux_min && humidity0 <= hum_max) {
    // Les blocs de code suivants sont conditionnés par l'état des cases à cocher
    if (activateHarpe1) {
      digitalWrite(harpe1, HIGH);
      delay(delayTime); // Utiliser delayTime
      digitalWrite(harpe1, LOW);
      delay(100);
      Serial.println("Harpe1");
    }

    if (activateHarpe2) {
      digitalWrite(harpe2, HIGH);
      delay(delayTime); // Utiliser delayTime
      digitalWrite(harpe2, LOW);
      delay(100);
      Serial.println("Harpe2");
    }

    if (activateHarpe3) {
      digitalWrite(harpe3, HIGH);
      delay(delayTime); // Utiliser delayTime
      digitalWrite(harpe3, LOW);
      delay(100);
      Serial.println("Harpe3");
    }

    if (activateHarpe4) {
      digitalWrite(harpe4, HIGH);
      delay(delayTime); // Utiliser delayTime
      digitalWrite(harpe4, LOW);
      delay(100);
      Serial.println("Harpe4");
    }

    if (activateHarpe5) {
      digitalWrite(harpe5, HIGH);
      delay(delayTime); // Utiliser delayTime
      digitalWrite(harpe5, LOW);
      delay(100);
      Serial.println("Harpe5");
    }

    if (activateHarpe6) {
      digitalWrite(harpe6, HIGH);
      delay(delayTime); // Utiliser delayTime
      digitalWrite(harpe6, LOW);
      delay(100);
      Serial.println("Harpe6");
    }
        }
         else {
      Serial.println("Going to sleep now");
      Serial.flush();
      esp_deep_sleep_start();
      Serial.println("This will never be printed");
    }
  }
}

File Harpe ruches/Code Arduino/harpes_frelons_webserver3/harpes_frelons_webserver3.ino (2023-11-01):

//####################### Ratamuse ###############################//
//################## ratamuse.pf@googlemail.com ##################//
//######################### October 2023 #########################//
//#################### ESP32 Devboard 3.3V  ######################//
//######################## Version 1.0.0 #########################//


#include "Arduino.h"
#include <Wire.h>
#include <WiFi.h>
#include <WebServer.h>
#include <Preferences.h>

// Set up WiFi access point
const char* ssid = "harpes";
const char* password = "123456789";

// Set up web server
WebServer server(80);

/*********************VEML7700*******************************/

#include "Adafruit_VEML7700.h"

Adafruit_VEML7700 veml = Adafruit_VEML7700();
float lux = 0;

/********************Sht4x*********************************/

#include <SensirionI2CSht4x.h>

SensirionI2CSht4x sht4x;
uint16_t error0;
float temperature0;
float humidity0;
float hum_max = 90;
float lux_min = 20;
char errorMessage[256];

/*********************Preferences***************************/

// Set up preferences
Preferences preferences;

/************************Define*****************************/

#define SDA_PIN 21
#define SCL_PIN 22
#define SDA_PIN1 27
#define SCL_PIN1 26

#define harpe1 17
#define harpe2 16
#define harpe3 4
#define harpe4 13
#define harpe5 19
#define harpe6 18
#define wifi 25
int customDelay = 1000;

#define uS_TO_S_FACTOR 1000000ULL /* Conversion factor for micro seconds to seconds */
#define TIME_TO_SLEEP 600         /* Time ESP32 will go to sleep (in seconds) */

bool startWebServer = false;
bool useHarpe1 = true;
bool useHarpe2 = true;
bool useHarpe3 = true;
bool useHarpe4 = true;
bool useHarpe5 = true;
bool useHarpe6 = true;

void setup() {
  pinMode(wifi, INPUT_PULLUP);

  if (digitalRead(wifi) == LOW) {
    // Connect to WiFi network
    startWebServer = true;
    pagehtml();
  } else {
    programme();
  }
}

void loop() {
  if (startWebServer) {
    LUX();
    sht();
    server.handleClient();
  } else {
    LUX();
    sht();

    if (lux >= lux_min && humidity0 <= hum_max) {
      if (useHarpe1) {
        digitalWrite(harpe1, HIGH);
        delay(customDelay);
        Serial.println("Harpe 1");
        digitalWrite(harpe1, LOW);
        delay(100);
      }
      if (digitalRead(wifi) == LOW) {
        ESP.restart();
      }
      if (useHarpe2) {
        digitalWrite(harpe2, HIGH);
        delay(customDelay);
        Serial.println("Harpe 2");
        digitalWrite(harpe2, LOW);
        delay(100);
      }
      if (digitalRead(wifi) == LOW) {
        ESP.restart();
      }
      if (useHarpe3) {
        digitalWrite(harpe3, HIGH);
        delay(customDelay);
        Serial.println("Harpe 3");
        digitalWrite(harpe3, LOW);
        delay(100);
      }
      if (digitalRead(wifi) == LOW) {
        ESP.restart();
      }
      if (useHarpe4) {
        digitalWrite(harpe4, HIGH);
        delay(customDelay);
        Serial.println("Harpe 4");
        digitalWrite(harpe4, LOW);
        delay(100);
      }
      if (digitalRead(wifi) == LOW) {
        ESP.restart();
      }
      if (useHarpe5) {
        digitalWrite(harpe5, HIGH);
        delay(customDelay);
        Serial.println("Harpe 5");
        digitalWrite(harpe5, LOW);
        delay(100);
      }
      if (digitalRead(wifi) == LOW) {
        ESP.restart();
      }
      if (useHarpe6) {
        digitalWrite(harpe6, HIGH);
        delay(customDelay);
        Serial.println("Harpe 6");
        digitalWrite(harpe6, LOW);
        delay(100);
      }
      if (digitalRead(wifi) == LOW) {
        ESP.restart();
      }
    } else {
      Serial.println("Going to sleep now");
      Serial.flush();
      esp_deep_sleep_start();
      Serial.println("This will never be printed");
    }
  }
}


/*****************************Intensité lumineuse en LUX****************************/

void LUX() {
  lux = veml.readLux(VEML_LUX_AUTO);
  Serial.print(lux, 2);
  Serial.println("lux");
}

/*****************************Valeur du capteur SHT41****************************/

void sht() {
  error0 = sht4x.measureHighPrecision(temperature0, humidity0);
  Serial.print(humidity0, 2);
  Serial.println("humidité");
}

void handleRoot() {
  String html = "<html><head><style>";
  html += "body { background-color: #F4D03F; font-family: Arial, sans-serif; }";
  html += "h1 { color: #E74C3C; text-align: center; font-size: 5vw; }";
  html += "p { color: #333333; font-size: 3vw; }";
  html += "label { color: #E74C3C; font-weight: bold; font-size: 3vw; }";
  html += "input[type='text'] { padding: 2vw; border: 0.5vw solid #FF6600; border-radius: 1vw; font-size: 2vw; }";
  html += "input[type='submit'] { padding: 2vw 4vw; background-color: #FF6600; color: #FFFFFF; border: none; border-radius: 1vw; font-size: 2vw; cursor: pointer; }";
  html += "</style>";
  html += "<meta http-equiv=\"refresh\" content=\"10\">";
  html += "</head><body>";
  html += "<h1>Harpes Ratamuse</h1>";
  html += "<p>Current humidity: " + String(humidity0) + "</p>";
  html += "<p>Current luminosity: " + String(lux) + "</p>";
  html += "<form action=\"/update\" method=\"POST\">";
  html += "<label for=\"hum_max\">Maximum humidity:</label>";
  html += "<input type=\"text\" id=\"hum_max\" name=\"hum_max\" value=\"" + String(hum_max) + "\">";
  html += "<br><br>";
  html += "<label for=\"lux_min\">Minimum luminosity:</label>";
  html += "<input type=\"text\" id=\"lux_min\" name=\"lux_min\" value=\"" + String(lux_min) + "\">";
  html += "<br><br>";
  html += "<label for=\"custom_delay\">Custom delay:</label>";
  html += "<input type=\"text\" id=\"custom_delay\" name=\"custom_delay\" value=\"" + String(customDelay) + "\">";
  html += "<br><br>";
  html += "<label for=\"harpe1\">Use Harpe 1:</label>";
  html += "<input type=\"checkbox\" id=\"harpe1\" name=\"harpe1\" " + String(useHarpe1 ? "checked" : "") + ">";
  html += "<br><br>";
  html += "<label for=\"harpe2\">Use Harpe 2:</label>";
  html += "<input type=\"checkbox\" id=\"harpe2\" name=\"harpe2\" " + String(useHarpe2 ? "checked" : "") + ">";
  html += "<br><br>";
  html += "<label for=\"harpe3\">Use Harpe 3:</label>";
  html += "<input type=\"checkbox\" id=\"harpe3\" name=\"harpe3\" " + String(useHarpe3 ? "checked" : "") + ">";
  html += "<br><br>";
  html += "<label for=\"harpe4\">Use Harpe 4:</label>";
  html += "<input type=\"checkbox\" id=\"harpe4\" name=\"harpe4\" " + String(useHarpe4 ? "checked" : "") + ">";
  html += "<br><br>";
  html += "<label for=\"harpe5\">Use Harpe 5:</label>";
  html += "<input type=\"checkbox\" id=\"harpe5\" name=\"harpe5\" " + String(useHarpe5 ? "checked" : "") + ">";
  html += "<br><br>";
  html += "<label for=\"harpe6\">Use Harpe 6:</label>";
  html += "<input type=\"checkbox\" id=\"harpe6\" name=\"harpe6\" " + String(useHarpe6 ? "checked" : "") + ">";
  html += "<br><br>";
  html += "<input type=\"submit\" value=\"Save\">";
  html += "</form>";
  html += "</body></html>";

  server.send(200, "text/html", html);
}
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

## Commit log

2023-09-28 Update PCB
    [Harpe ruches-B_Cu.gbr, Harpe ruches-B_Mask.gbr, Harpe ruches-B_Paste.gbr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]
2023-09-28 Revert "Update PCB"
    This reverts commit 88c6fc853c4fb05f29f730f761ab4a511938047f.
    [Harpe ruches-B_Cu.gbr, Harpe ruches-B_Mask.gbr, Harpe ruches-B_Paste.gbr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]
2023-10-05 code arduino
2023-12-11 code & image update
    [Resine HT.SLDPRT, Resine HT.STL]
2023-12-12 pcb updated
    [Harpe_ESP32-B_Cu.gbr, Harpe_ESP32-B_Mask.gbr, Harpe_ESP32-B_Paste.gbr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]
2023-12-13 dessin update
    [Harpe_BOM_PCBWay.xlsx, Sample_BOM_PCBWay.xlsx]
2024-07-20 pcb bas update
    [05_03_032.SLDPRT, 36_01_032.SLDPRT, Harpe 2.0.SLDASM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]
